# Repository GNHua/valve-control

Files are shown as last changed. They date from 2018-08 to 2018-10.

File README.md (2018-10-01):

# valve-control

Use Arduino Uno to control solenoid valves.  
Follow the steps below to set up your own valve control station.

## Purchase

### Solenoid Valves

* [Clippard, E310C-2C012, 10 mm N-C 3-way Valve, In-line Connector w/LED, 0.030" Orifice, 1.3W, 12 VDC](http://www.clippard.com/part/E310C-2C012)
* [Valve connector cable](http://www.clippard.com/products/electronic-valve-10mm-connector)
* [Manifold](http://www.clippard.com/products/electronic-valve-10mm-manifolds)

Details can be found on page 215-221 in [Clippard Full-line Catalog](http://www.clippard.com/downloads/PDF_Documents/Clippard%20Full%20Line%20Catalog/Clippard%20Full-Line%20Catalog.pdf)

### Send [PCB design](https://github.com/GNHua/valve-control/raw/master/pcb_layout/plots.zip) Out For Manufacturing

* Highly recommend [JLCPCB](https://jlcpcb.com/). Fabrication and shipping took ~1 week for me in the U.S.
* If you choose JLCPCB, go [here](https://jlcpcb.com/quote), upload [plots.zip](pcb_layout/plots.zip), and leave everything else as default.
* If you have access to a PCB baking oven, buying a SMT-Stencil will save you a lot of time for soldering. If not, all the components can still be soldered by hand.

| Top Layer | Bottom Layer |
| --- | --- |
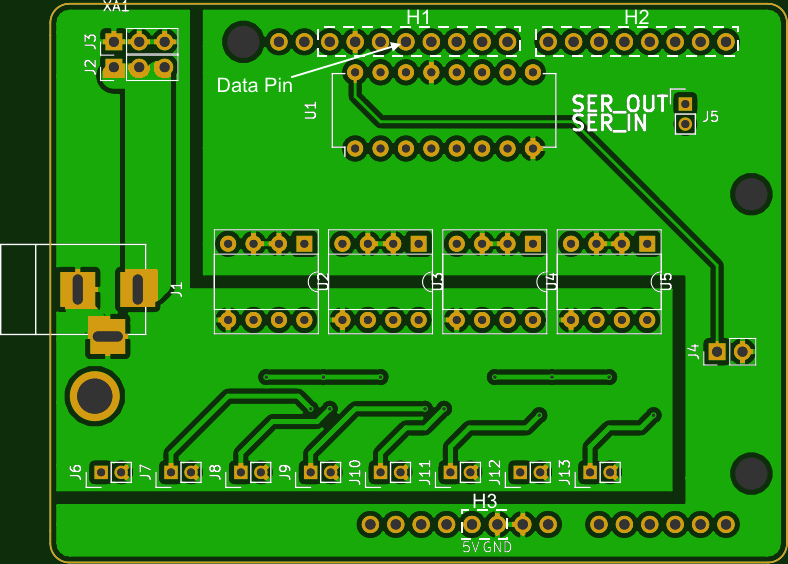
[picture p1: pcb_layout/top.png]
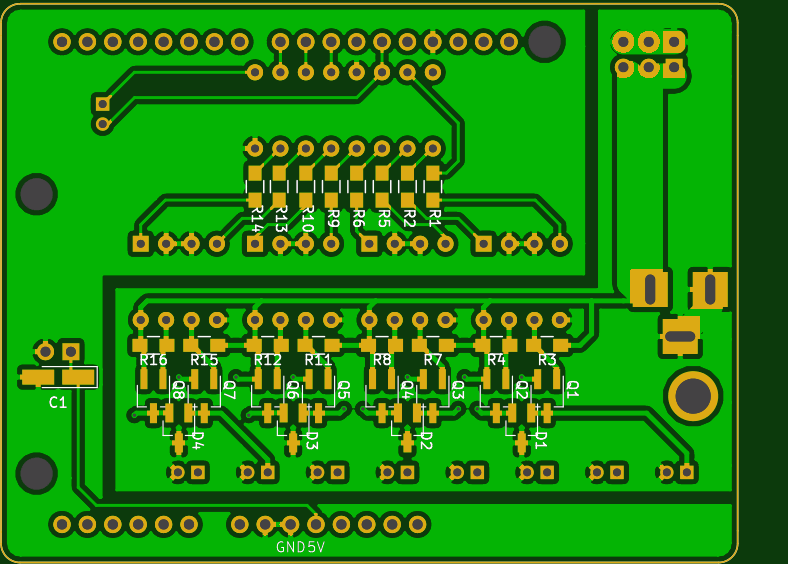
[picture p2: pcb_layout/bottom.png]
|  |  |

### Electrical Components To Buy

| Part | Label on PCB | Qty. (per PCB) | Purchase |
| ---- | :--- | :---: | :---: |
| [Shift register, SN74HC595N](https://www.digikey.com/product-detail/en/texas-instruments/SN74HC595N/296-1600-5-ND/277246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) | plug on the DIP socket (U1) | 1 | [link](https://www.digikey.com/product-detail/en/texas-instruments/SN74HC595N/296-1600-5-ND/277246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)
| [Optoisolator, HCPL 2731](https://www.digikey.com/product-detail/en/on-semiconductor/HCPL2731/HCPL2731QT-ND/31642) | plug on the DIP sockets (U2-U5) | 4 | [link](https://www.digikey.com/product-detail/en/on-semiconductor/HCPL2731/HCPL2731QT-ND/31642) |
| [Resistor, 2.32 k&Omega;, package 0805](https://www.digikey.com/product-detail/en/stackpole-electronics-inc/RMCF0805FT2K32/RMCF0805FT2K32DKR-ND/1943295) | R1-R16 | 16 | [link](https://www.digikey.com/product-detail/en/stackpole-electronics-inc/RMCF0805FT2K32/RMCF0805FT2K32DKR-ND/1943295) |
| [Common anode diode](https://www.digikey.com/product-detail/en/diodes-incorporated/BAT54AT-7-F/BAT54AT-FDICT-ND/821941) | D1-D4 | 4 | [link](https://www.digikey.com/product-detail/en/diodes-incorporated/BAT54AT-7-F/BAT54AT-FDICT-ND/821941) |
| [PMOS](https://www.digikey.com/product-detail/en/toshiba-semiconductor-and-storage/SSM3J338RLF/SSM3J338RLFCT-ND/5810258) | Q1-Q8 | 8 | [link](https://www.digikey.com/product-detail/en/toshiba-semiconductor-and-storage/SSM3J338RLF/SSM3J338RLFCT-ND/5810258) |
| [1 uF capacitor, package 0805, voltage rating 10V](https://www.digikey.com/product-detail/en/yageo/CC0805KKX7R6BB105/311-1458-1-ND/2833764) | C1 | 1 | [link](https://www.digikey.com/product-detail/en/yageo/CC0805KKX7R6BB105/311-1458-1-ND/2833764) |
| [DIP socket, 2x8](https://www.digikey.com/product-detail/en/assmann-wsw-components/A-16-LC-TT/AE9992-ND/821746) | U1 | 1 | [link](https://www.digikey.com/product-detail/en/assmann-wsw-components/A-16-LC-TT/AE9992-ND/821746) |
| [DIP socket, 2x4](https://www.digikey.com/product-detail/en/assmann-wsw-components/A-08-LC-TT/AE9986-ND/821740) | U2-U5 | 4 | [link](https://www.digikey.com/product-detail/en/assmann-wsw-components/A-08-LC-TT/AE9986-ND/821740) |
| [Stacking headers](https://www.digikey.com/products/en?mpart=85&v=1528) | J2-J4, H1, H2 | 1 | [link](https://www.digikey.com/products/en?mpart=85&v=1528) |
| [Connector, Molex 50212-8000](https://www.digikey.com/product-detail/en/molex-llc/50212-8000/WM4561CT-ND/2524899) | N/A | 18 | [link](https://www.digikey.com/product-detail/en/molex-llc/50212-8000/WM4561CT-ND/2524899) |
| [Connector housing, Molex 0873690200](https://www.digikey.com/product-detail/en/molex-llc/0873690200/WM10118-ND/3264531) | N/A | 9 | [link](https://www.digikey.com/product-detail/en/molex-llc/0873690200/WM10118-ND/3264531) |
| [JST header, Molex 0894010210](https://www.digikey.com/products/en?keywords=0894010210) | J5-J13 | 9 | [link](https://www.digikey.com/products/en?keywords=0894010210) |
| [2.5 mm barrel jack, 5A max, CUI PJ-057BH ](https://www.digikey.com/product-detail/en/cui-inc/PJ-057BH/CP-057BH-ND/1644602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) | J1 | 1 for each setup | [link](https://www.digikey.com/product-detail/en/cui-inc/PJ-057BH/CP-057BH-ND/1644602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) |

## Download

Download [zip](https://github.com/GNHua/valve-control/archive/master.zip) and extract all files.

## Prepare Software

### Flash Arduino Uno

* Connect an Arduino Uno to computer via USB
* Download and Install [Arduino IDE](https://www.arduino.cc/en/Main/Software)
* Open `arduino_valve_control.ino` in `arduino_valve_control` folder with Arduino IDE
* Select USB port: `Tools` > `Port`
* Click `Upload` (the right arrow at the top left corner)
* Wait for uploading to complete

### Python

* Download and Install Python 3.6
  * The Python distribution, [Anaconda](https://www.anaconda.com/download) is recommended, because it comes with pre-installed packages. 
  * Note: On Windows, the directory of installed Python must be added to environment variable. 
* Install Python dependencies
  * Windows: double click `platforms/windows/setup.bat`
  * MacOSX: `$ bash <path to>/platforms/macosx/setup.sh`

## Soldering

(ADD photos of top and bottom layer after soldering)

Solder all the components according to the [table above](#Electrical-Components-To-Buy). The surface mount components are soldered to the bottom layer, while the rest are mounted on the top layer.

### Stacking Headers

In the [table above](#Electrical-Components-To-Buy), the [stacking headers](https://www.digikey.com/products/en?mpart=85&v=1528) contains the following headers.

| Stacking Header | Label on PCB | Qty. |
| --- | :--- | :--: |
| 1 x 10 | cut out a 1x2 for J4 | 1 |
| 1 x  8 | H1, H2 | 2 |
| 1 x  6 | | 2 |
| 2 x  3 | J2+J3 | 1 |

### H3 - 5V and GND

Because the JST headers at J11 and J12 block H3 on the top layer, I would do the following:

1. Cut a 1x2 stacking header out of an unused one
2. Solder it on H3 from the bottom layer
3. Cut off the female portion on the top layer
4. Put more solder from the top layer

### Barrel Jack

Each setup only needs one barrel jack to connect to a 12 V power supply. The barrel jack can be soldered on any one of the boards.

## Assembly

### Shift Register and Optoisolators

(The images shown below are all taken for the previous PCB design, which is marginally different from the current design.)

After soldering, plug the shift register and optoisolators into their corresponding DIP sockets. Refer to the following image for their orientation.

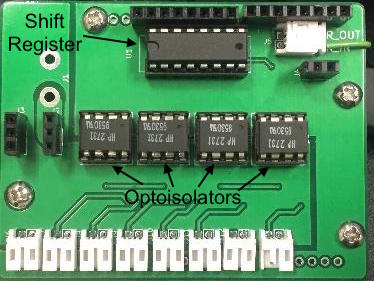
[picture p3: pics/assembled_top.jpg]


### Stacking PCBs

#### For the inpatient

1. Bend or remove the data pins on all boards except Board 1. See the left image below.
2. Make a connector for serial input and serial output. See the right image below.
3. Stack the PCBs and plug in the connector just made.

| Data Pin | Serial Input/Output |
| --- | --- |
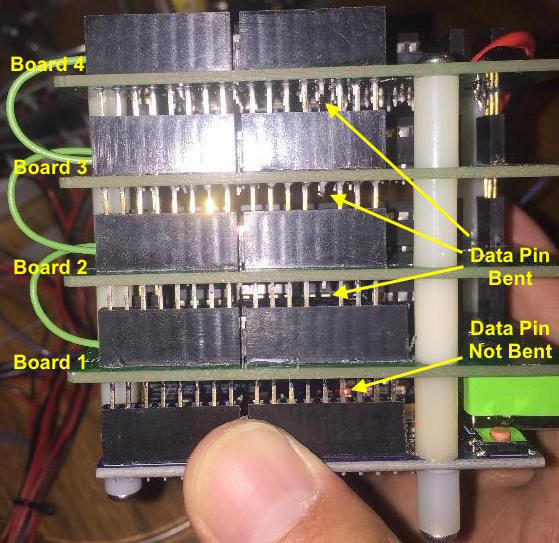
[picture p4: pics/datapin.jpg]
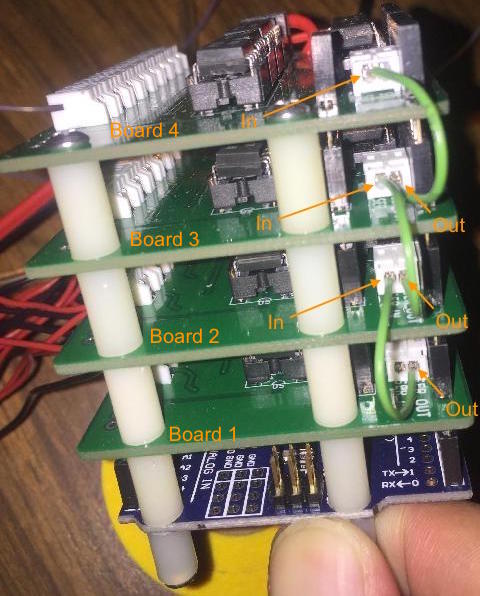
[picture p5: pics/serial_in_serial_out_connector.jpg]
|  |  |

#### Details

In the images above, there are 4 boards stacked on an Arduino Uno.  
Each board provides 8 solenoid valve connectors, and the current design supports up to 6 boards.  
**Before putting the boards together, the data pins on all boards except Board 1 must be bent or removed.**
This is because the data pin connects to the serial input of shift register.
On Board 1, the shift register receives data from the Arduino directly.
For the Board 2-n, their shift registers must have its serial input connected to the serial output of board right beneath it.

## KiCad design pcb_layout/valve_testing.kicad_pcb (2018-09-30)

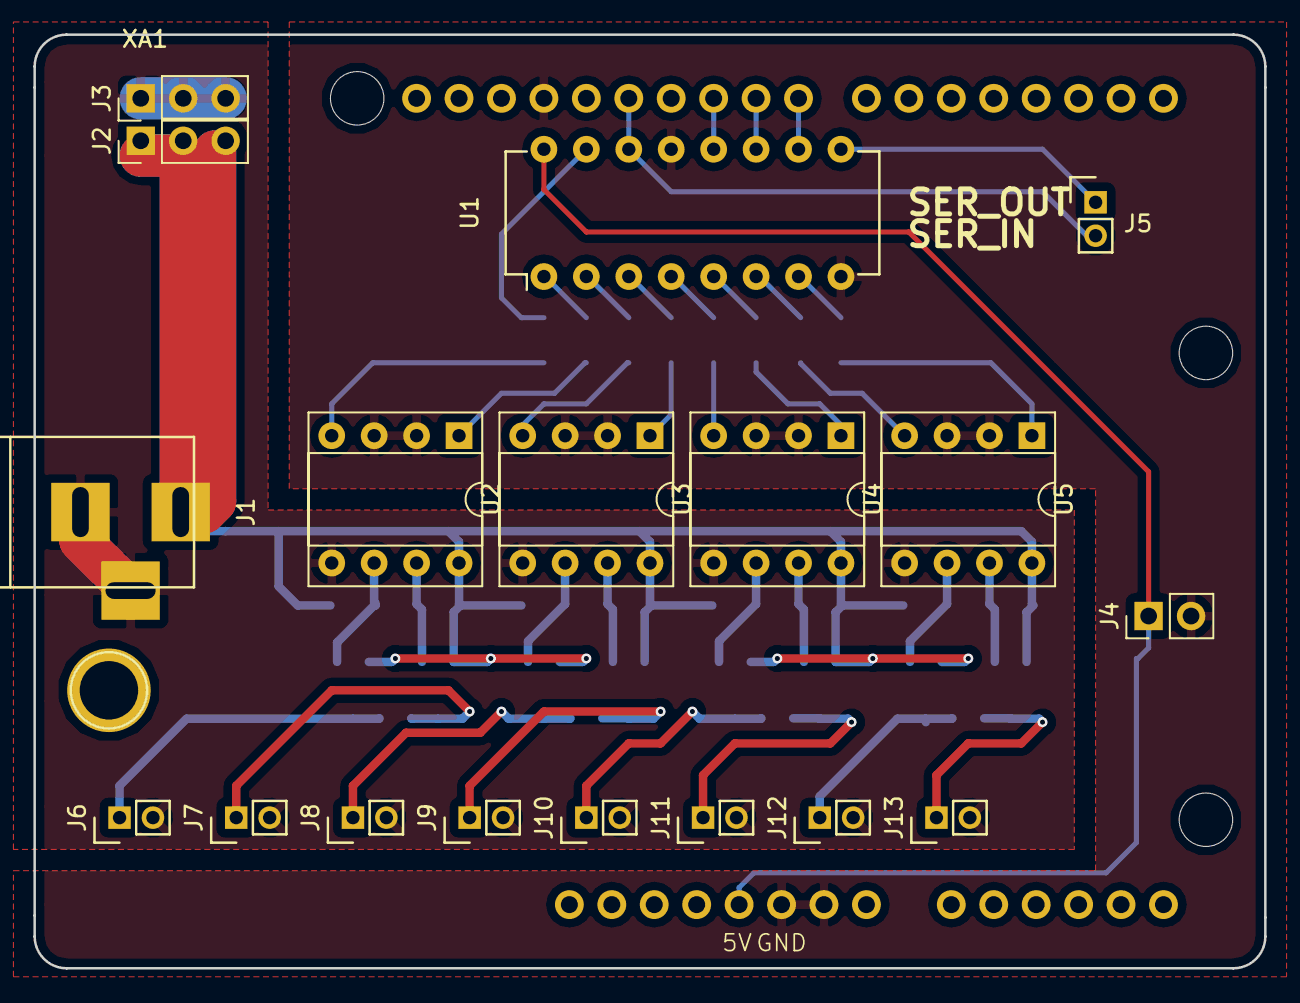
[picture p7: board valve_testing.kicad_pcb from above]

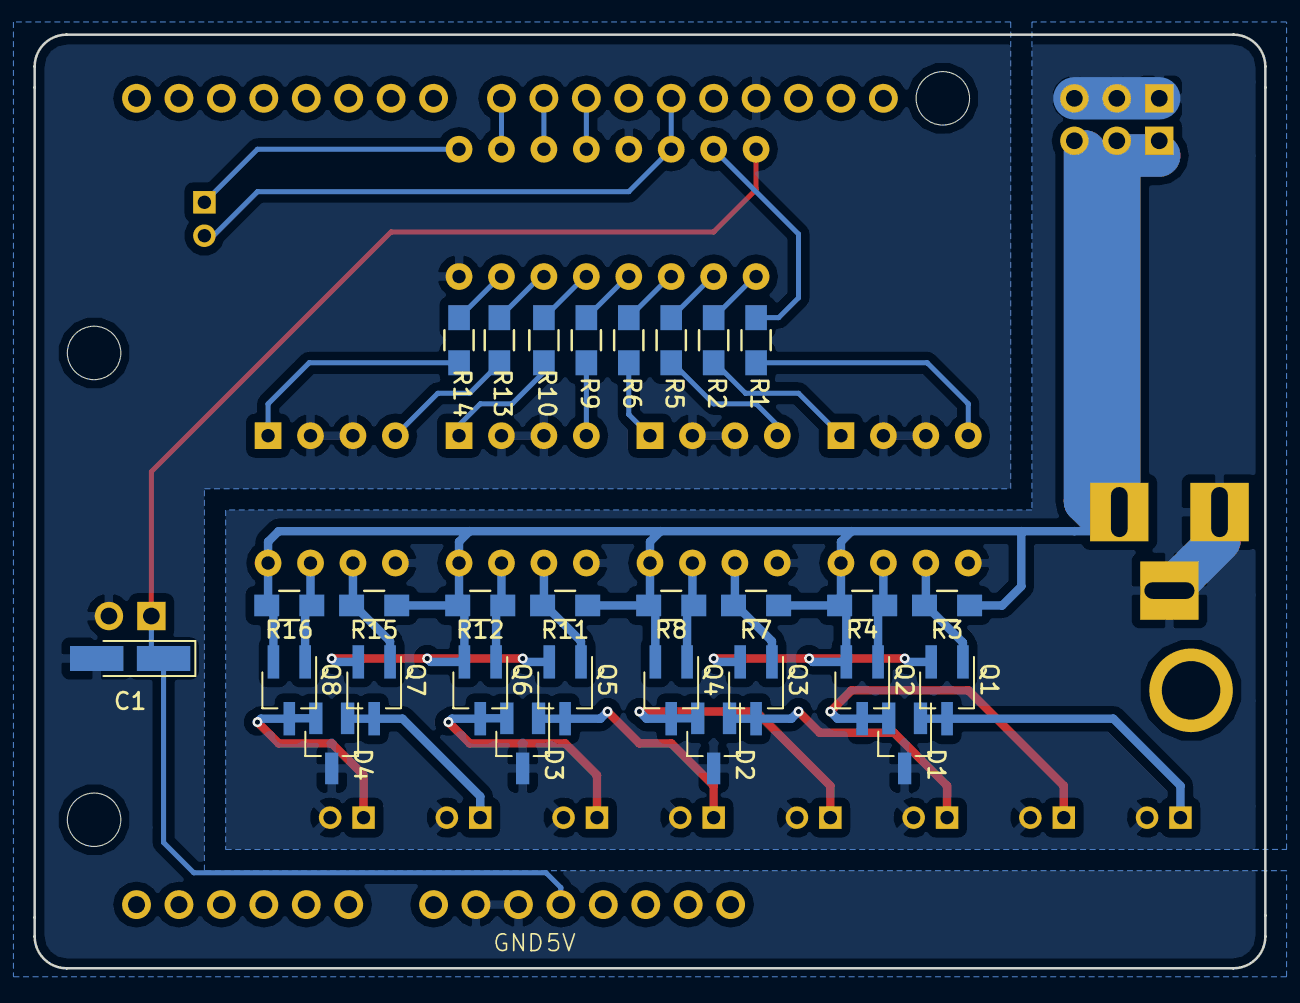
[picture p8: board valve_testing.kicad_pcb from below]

Board: 2 copper layers, 73.7 x 55.9 mm, 48 parts (29 on the bottom side), 40 nets.

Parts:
C1: 1u; CP_Tantalum_Case-A_EIA-3216-18_Hand
D1, D2, D3, D4: D_Schottky_x2_ACom_KKA; SOT-23_Handsoldering
J1: Barrel_Jack; BARREL_JACK
J2, J3: Conn_01x04; Pin_Header_Straight_1x03_Pitch2.54mm
J4: Conn_01x02; Pin_Header_Straight_1x02_Pitch2.54mm
J5, J6, J7, J8, J9, J10, J11, J12, J13: Conn_01x02; Pin_Header_Straight_1x02_Pitch2.00mm
Q1, Q2, Q3, Q4, Q5, Q6, Q7, Q8: Q_PMOS_GSD; SOT-23W_Handsoldering
R1, R2, R3, R4, R5, R6, R7, R8, R9, R10, R11, R12, R13, R14, R15, R16: 2.32k; R_0805_HandSoldering
U1: 74HC595; DIP-16_W7.62mm
U2, U3, U4, U5: HCPL2731; DIP-8_W7.62mm_Socket
XA1: Arduino_Uno_Shield

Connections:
/QA: R1.1, U1.15
/QB: R2.1, U1.1
/QC: R5.1, U1.2
/QD: R6.1, U1.3
/QE: R9.1, U1.4
/QF: R10.1, U1.5
/QG: R13.1, U1.6
/QH: R14.1, U1.7
/SRCLR: U1.10, XA1.D8
/clockPin: U1.11, XA1.D9
/dataPin: J5.2, U1.14, XA1.D12
/latchPin: U1.12, XA1.D10
GND: C1.2, D1.3, D2.3, D3.3, D4.3, J1.2, J1.3, J3.1, J3.2, J3.3, J4.2, J6.2, J7.2, J8.2, J9.2, J10.2, J11.2, J12.2, J13.2, U1.8, U1.13, U2.2, U2.3, U2.5, U3.2, U3.3, U3.5, U4.2, U4.3, U4.5, U5.2, U5.3, U5.5, XA1.GND1, XA1.GND2, XA1.GND3
unnamed: D1.1, J6.1, Q1.3
unnamed: D1.2, J7.1, Q2.3
unnamed: D2.1, J8.1, Q3.3
unnamed: D2.2, J9.1, Q4.3
unnamed: D3.1, J10.1, Q5.3
unnamed: D3.2, J11.1, Q6.3
unnamed: D4.1, J12.1, Q7.3
unnamed: D4.2, J13.1, Q8.3
unnamed: J5.1, U1.9
unnamed: Q1.1, R3.2, U2.6
unnamed: Q2.1, R4.2, U2.7
unnamed: Q3.1, R7.2, U3.6
unnamed: Q4.1, R8.2, U3.7
unnamed: Q5.1, R11.2, U4.6
unnamed: Q6.1, R12.2, U4.7
unnamed: Q7.1, R15.2, U5.6
unnamed: Q8.1, R16.2, U5.7
unnamed: R1.2, U2.4
unnamed: R2.2, U2.1
unnamed: R5.2, U3.4
unnamed: R6.2, U3.1
unnamed: R9.2, U4.4
unnamed: R10.2, U4.1
unnamed: R13.2, U5.4
unnamed: R14.2, U5.1
VCC: C1.1, J4.1, U1.16, XA1.5V1
Vcc_12V: J1.1, J2.1, J2.2, J2.3, Q1.2, Q2.2, Q3.2, Q4.2, Q5.2, Q6.2, Q7.2, Q8.2, R3.1, R4.1, R7.1, R8.1, R11.1, R12.1, R15.1, R16.1, U2.8, U3.8, U4.8, U5.8

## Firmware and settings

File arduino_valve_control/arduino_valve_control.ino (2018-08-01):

#include <EEPROM.h>

#include "SoftReset.h"
#include "defaults.h"

#define MYPORT PORTB
#define SRCLR 8
#define dataPin 12
#define clockPin 9
#define latchPin 10
#define SRCLRBitLoc (SRCLR-8)
#define dataPinBitLoc (dataPin-8)
#define clockPinBitLoc (clockPin-8)
#define latchPinBitLoc (latchPin-8)

uint8_t regNum;    // number of registers used
char* currentState;        // keep track of shift register outputs
char* masks;
char* operations;         // 100 different operations max
uint8_t* phase;      // a list of phase describes the valve actuating sequence
uint8_t* beforePhase;
uint8_t* afterPhase;
volatile uint16_t currentPhaseIndex;        // current phase
uint8_t totalPhases;     // total number of phases
uint8_t totalBeforePhases;
uint8_t totalAfterPhases;
volatile uint32_t currentCycle = 0;
uint32_t totalCycles = 0;
bool longTimerEnabled;
uint32_t intervalMillis;
uint32_t previousMillis;

const uint8_t serStrLen = 28;   // max length of serial input string, baudrate 115200 for 2 ms
char serInStr[ serStrLen ];     // array that will hold the serial input string

void fastShiftOut(char* data, uint8_t length)
{
  // reset clock pin and latch pin
  MYPORT &= ~(1 << latchPinBitLoc);
  
  for(uint8_t i=0; i<length; i++) {
    for(int8_t j=7; j>=0; j--) {
      MYPORT &= ~(1 << clockPinBitLoc);
      
      // set data pin
      char dataBit = (data[i] >> j) & B00000001;
      // change the data pin
      MYPORT ^= (MYPORT ^ -(uint8_t)dataBit) & (1 << dataPinBitLoc);
      
      MYPORT |= (1 << clockPinBitLoc);
    }
  }
  
  // create a rising edge at latch pin
  MYPORT |= (1 << latchPinBitLoc);
}

void controlValves(char* data, char* mask, uint8_t length)
{
  for(uint8_t i=0; i<length; i++) {
    data[i] &= mask[i];
    currentState[i] &= ~mask[i];
    currentState[i] |= data[i];
  }
  
  fastShiftOut(currentState, length);
}

void start()
{
  // do nothing if it is already running
  if (((TIMSK1 >> OCIE1A) & B00000001) || longTimerEnabled) {
    return ;
  }

  runBeforeAfterPhase(beforePhase, totalBeforePhases);

  if (totalPhases) {
    currentPhaseIndex = 0;
    currentCycle = 0;
    if (intervalMillis <= 200) {
      float freq = 1000 / intervalMillis;
      noInterrupts();
      OCR1A = (uint16_t)(1.6e7 / 64 / freq);
      TCNT1 = 0;
      TIMSK1 |= (1 << OCIE1A);
      interrupts();
    } else {
      longTimerEnabled = true;
      previousMillis = millis();
    }
  }
}

/////////////////////////////////////////////////

// use hardware timer for interval equal to or below 200 ms
ISR(TIMER1_COMPA_vect)  // timer compare interrupt service routine
{
  controlValves(operations+phase[currentPhaseIndex]*regNum, masks+phase[currentPhaseIndex]*regNum, regNum);
  currentPhaseIndex++;

  if (currentPhaseIndex >= totalPhases) {
    currentPhaseIndex = 0;
    currentCycle++;
  }

  // disable timer compare interrupt if all cycles are done
  if (totalCycles != 0 && currentCycle >= totalCycles) {
    TIMSK1 &= ~(1 << OCIE1A);
    currentCycle = 0;
    runBeforeAfterPhase(afterPhase, totalAfterPhases);
  }
}

// use long timer for interval above 200 ms
void runLongTimer()
{
  uint32_t currentMillis = millis(); // grab current time
  if (longTimerEnabled && (uint32_t)(currentMillis - previousMillis) >= intervalMillis) {
    controlValves(operations+phase[currentPhaseIndex]*regNum, masks+phase[currentPhaseIndex]*regNum, regNum);
    currentPhaseIndex++;
    
    // save the "current" time
    previousMillis = currentMillis;
    
    if (currentPhaseIndex >= totalPhases) {
      currentPhaseIndex = 0;
      currentCycle++;
    }
    
    // disable long timer if all cycles are run
    if (totalCycles != 0 && currentCycle >= totalCycles) {
      longTimerEnabled = false;
      currentCycle = 0;
      runBeforeAfterPhase(afterPhase, totalAfterPhases);
    }
  }
}
/////////////////////////////////////////////////

void runBeforeAfterPhase(uint8_t* phase, uint8_t length)
{
  for(uint8_t i=0; i<length; i++) {
    controlValves(operations+phase[i]*regNum, masks+phase[i]*regNum, regNum);
    delay(intervalMillis);
  }
}

void stop()
{
  TIMSK1 &= ~(1 << OCIE1A);
  longTimerEnabled = false;
  runBeforeAfterPhase(afterPhase, totalAfterPhases);

  Serial.write((char*)(&currentCycle), sizeof(currentCycle));
  Serial.write(currentState, regNum);
  Serial.println();
  currentCycle = 0;
}

void clearShiftRegister()
{
  // do nothing if it is already running
  if (((TIMSK1 >> OCIE1A) & B00000001) || longTimerEnabled) {
    return ;
  }
  
  MYPORT &= ~(1 << latchPinBitLoc);
  MYPORT &= ~(1 << clockPinBitLoc);
  MYPORT &= ~(1 << SRCLRBitLoc);
  MYPORT |= (1 << clockPinBitLoc);
  MYPORT |= (1 << SRCLRBitLoc);
  MYPORT |= (1 << latchPinBitLoc);
  
  // reset currentState
  memset(currentState, 0, regNum);
}

void clear()
{
  // do nothing if it is already running
  if (((TIMSK1 >> OCIE1A) & B00000001) || longTimerEnabled) {
    return ;
  }
  
  clearShiftRegister();
  uint8_t operationNum = EEPROM.read(OPERATION_NUM_ADDR);
  uint8_t phaseNum = EEPROM.read(PHASE_NUM_ADDR);
  uint8_t beforePhaseNum = EEPROM.read(BEFORE_PHASE_NUM_ADDR);
  uint8_t afterPhaseNum = EEPROM.read(AFTER_PHASE_NUM_ADDR);
  memset(operations, 0, operationNum*regNum);
  memset(masks, 0, operationNum*regNum);
  memset(phase, 0, phaseNum);
  memset(beforePhase, 0, beforePhaseNum);
  memset(afterPhase, 0, afterPhaseNum);
  
  currentPhaseIndex = 0;        // current phase
  totalPhases = 0;              // total number of phases
  totalBeforePhases = 0;
  totalAfterPhases = 0;
  currentCycle = 0;
  totalCycles = 0;
}

void setup()
{
  uint8_t flag = EEPROM.read(VERSION_ADDR);
  if (flag != VERSION) {
    EEPROM.update(VERSION_ADDR, (byte)VERSION);
    EEPROM.update(REG_NUM_ADDR, (byte)REG_NUM);
    EEPROM.update(OPERATION_NUM_ADDR, (byte)OPERATION_NUM);
    EEPROM.update(PHASE_NUM_ADDR, (byte)(PHASE_NUM));
    EEPROM.update(BEFORE_PHASE_NUM_ADDR, (byte)(BEFORE_PHASE_NUM));
    EEPROM.update(AFTER_PHASE_NUM_ADDR, (byte)(AFTER_PHASE_NUM));
  }
  
  pinMode(SRCLR, OUTPUT);
  MYPORT |= (1 << SRCLRBitLoc);
  
  pinMode(dataPin,  OUTPUT);
  pinMode(clockPin, OUTPUT);
  pinMode(latchPin, OUTPUT);
  
  // initialize timer1 
  noInterrupts();     // disable all interrupts
  TCCR1A = 0;
  TCCR1B = 0;
  TCCR1B |= (1 << WGM12);                 // CTC mode
  TCCR1B |= (1 << CS11) | (1 << CS10);    // 64 prescaler 
  TIMSK1 &= ~(1 << OCIE1A);               // disable timer compare interrupt
  interrupts();                           // enable all interrupts
  
  longTimerEnabled = false;

  regNum = EEPROM.read(REG_NUM_ADDR);
  uint8_t operationNum = EEPROM.read(OPERATION_NUM_ADDR);
  uint8_t phaseNum = EEPROM.read(PHASE_NUM_ADDR);
  uint8_t beforePhaseNum = EEPROM.read(BEFORE_PHASE_NUM_ADDR);
  uint8_t afterPhaseNum = EEPROM.read(AFTER_PHASE_NUM_ADDR);
  currentState = (char*)malloc(regNum);
  masks = (char*)malloc(operationNum*regNum);
  operations = (char*)malloc(operationNum*regNum);
  phase = (uint8_t*)malloc(phaseNum); 
  beforePhase = (uint8_t*)malloc(beforePhaseNum);
  afterPhase = (uint8_t*)malloc(afterPhaseNum);
  clear();
  
  Serial.begin(115200);
  delay(2000); //To allow time for serial port to begin
}

void loop()
{
  GetSerialInput();
  runLongTimer();
}

void GetSerialInput() {
  uint8_t strSize = readSerialString();
  if (strSize) {
    switch (serInStr[0]) {
      case 0x00: // send the number of shift registers
      {
        // byte 1: regNum
        if (regNum != EEPROM.read(REG_NUM_ADDR)) {
          EEPROM.update(REG_NUM_ADDR, serInStr[1]);
          regNum = EEPROM.read(REG_NUM_ADDR);
          soft_restart();
        }
        break;
      }
      case 0x01: // send the total phase number in one cycle
        // byte 1: totalPhases
        // byte 2: totalBeforePhases
        // byte 3: totalAfterPhases
        memcpy(&totalPhases, serInStr+1, sizeof(totalPhases));
        memcpy(&totalBeforePhases, serInStr+2, sizeof(totalBeforePhases));
        memcpy(&totalAfterPhases, serInStr+3, sizeof(totalAfterPhases));
        break;
      case 0x02: // send data in `operations`
      {
        // byte 1: offset in `operations`
        // byte 2-(2+regNum): data
        // byte (2+regNum)-(2+regNum*2): mask
        uint8_t i = serInStr[1];
        memcpy(operations+i*regNum, serInStr+2, regNum);
        memcpy(masks+i*regNum, serInStr+2+regNum, regNum);
        break;
      }
      case 0x03: // send data in `phase`
      {
        // byte 1: offset in `phase`; byte 2-?: data
        uint8_t i = serInStr[1];
        memcpy(phase+i, serInStr+2, strSize-2);
        break;
      }
      case 0x04: // send data in `beforePhase`
      {
        // byte 1: offset in `beforePhase`; byte 2-?: data
        uint8_t i = serInStr[1];
        memcpy(beforePhase+i, serInStr+2, strSize-2);
        break;
      }
      case 0x05: // send data in `afterPhase`
      {
        // byte 1: offset in `afterPhase`; byte 2-?: data
        uint8_t i = serInStr[1];
        memcpy(afterPhase+i, serInStr+2, strSize-2);
        break;
      }
      case 0x06: // start
      {
        // byte 1-4: totalCycles; byte 5-8: intervalMillis
        memcpy(&totalCycles, serInStr+1, sizeof(totalCycles));
        memcpy(&intervalMillis, serInStr+1+sizeof(totalCycles), sizeof(intervalMillis));
        start();
        break;
      }
      case 0x07: // stop
        stop();
        break;
      case 0x08: // control valves
      {
        // byte 1-(1+regNum): valve controls 
        // byte (1+regNum)-(1+regNum*2): mask
        controlValves(serInStr+1, serInStr+1+regNum, regNum);
        break;
      }
      case 0x09: // clear shift register outputs
      {
        clearShiftRegister();
        break;
      }
      case 0x0A:
      {
        clear();
        break;
      }
      case 0x0B:
      {
        uint8_t addr = serInStr[1];
        for(uint8_t i=2; i<strSize; i++) {
          EEPROM.update(addr, serInStr[i]);
          addr++;
        }
        soft_restart();
        break;
      }
      case 0x0C:
      {
        soft_restart();
        break;
      }
      case 0x0D:
      {
        Serial.write(currentState, regNum);
        Serial.write((char*)(&totalCycles), sizeof(totalCycles));
        Serial.write((char*)(&currentCycle), sizeof(currentCycle));
        Serial.println();
        break;
      }
      case 0x0E:
      {
        for(uint8_t i=0; i<256; i++) {
          byte res = EEPROM.read(i);
          if (res == 0xFF) {
            break;
          } else {
            Serial.write(res);
          }
        }
        Serial.println();
        break;
      }
      default:
        break;
    }
  }
}

uint8_t readSerialString() {
  if(!Serial.available()) {
    return 0;
  }
  delay(2);  // wait a little for serial data
  memset( serInStr, 0, sizeof(serInStr) ); // set it all to zero (look up Arduino memset function)
  uint8_t i = 0;
  while(Serial.available() && i<serStrLen ) {
    serInStr[i] = Serial.read();   // FIXME: doesn't check buffer overrun
    i++;
  }

  return i;  // return number of chars read
} //readSerialString

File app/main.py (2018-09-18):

import os
import sys
from PyQt5 import QtWidgets, uic
import serial.tools.list_ports
import urllib.request
import glob
import shutil
import zipfile
import webbrowser

from app import __version__
from app.ui.connect import UsbPortsTableDialog
from app.ui.flow_layout import FlowLayout
from app.ui.built_in_program_dialog import ToggleValveDialog, FivePhasePumpDialog
from app.valve_control import ValveControlDevice, ToggleValveCycle, FivePhasePumpCycle

APP_DIR = os.path.dirname(os.path.abspath(__file__))
ROOT_DIR = os.path.abspath(os.path.join(APP_DIR, '..'))
Ui_MainWindow, QMainWindow = uic.loadUiType(os.path.join(APP_DIR, 'ui', 'main.ui'))


class MainWindow(QMainWindow, Ui_MainWindow):

    def __init__(self):
        super().__init__()
        self.setupUi(self)
        self.flowLayoutValveControl = FlowLayout(parent=self.frameValveControl)
        with open(os.path.join(APP_DIR, 'ui', 'style_sheet.txt'), 'r') as f:
            styleSheet = f.read()
        self.setStyleSheet(styleSheet)

        self.dir = APP_DIR

    def getUsbPort(self):
        ports = serial.tools.list_ports.comports()
        dialog = UsbPortsTableDialog(ports=ports)
        if dialog.exec_() == QtWidgets.QDialog.Accepted:
            index = dialog.tableViewUsbPorts.selectedIndexes()[0]
            if index:
                port = ports[index.row()].device
                self.setDevice(port=port)
            else:
                QtWidgets.QMessageBox.critical(
                    self,
                    'Warning!',
                    'Please select a USB port\n',
                    QtWidgets.QMessageBox.Ok)
                self.getUsbPort()
        else:
            sys.exit()

    def setDevice(self, port):
        self.device = ValveControlDevice(port=port)
        regNum = self.device.settings['REG_NUM']
        for i in range(1, 8*regNum+1):
            checkBox = QtWidgets.QCheckBox(str(i))
            self.flowLayoutValveControl.addWidget(checkBox)
            checkBox.toggled[bool].connect(self.addValveControl(i))
            self.__dict__[f'checkBoxValve{i}'] = checkBox
        self.__dict__[f'actionSR{regNum}'].setChecked(True)
        self.menuSerial.setTitle(f'Port: "{port}"')
        self.connectUi()

    def addValveControl(self, i):
        def func(valveOn):
            self.device.controlSingleValve(i, valveOn)
        return func

    def connectUi(self):
        self.actionGroupSR = QtWidgets.QActionGroup(self.menuShift_Register)
        for i in range(1, 7):
            self.actionGroupSR.addAction(self.__dict__[f'actionSR{i}'])

        self.toolButtonProgram.clicked.connect(self.uploadProgram)
        self.pushButtonStart.clicked.connect(self.start)
        self.pushButtonStop.clicked.connect(self.stop)
        self.pushButtonLoadBuiltIn.clicked.connect(self.loadBuiltInProgram)
        self.actionOpen.triggered.connect(self.uploadProgram)
        self.actionClose.triggered.connect(self.close)
        self.actionRestart_Device.triggered.connect(self.restartDevice)
        self.actionTurn_Off_All.triggered.connect(self.clear)
        self.actionStart.triggered.connect(self.start)
        self.actionStop.triggered.connect(self.stop)
        self.actionGroupSR.triggered.connect(self.changeSR)
        self.actionReset_Input.triggered.connect(self.serialResetInput)
        self.actionReset_Output.triggered.connect(self.serialResetOutput)
        self.actionDocumentation.triggered.connect(self.openGithubRepo)
        self.actionUpdate.triggered.connect(self.update)

    def uploadProgram(self):
        fn, _ = QtWidgets.QFileDialog.getOpenFileName(self, 'Open File', self.dir, 'text (*.txt)')
        self.dir = os.path.dirname(fn)
        if fn:
            wrongLines = self.device.makeProgrammableCycle(fn)
            if wrongLines:
                wrongLines = ', '.join(list(map(str, self.device.programmableCycle.wrongLines)))
                QtWidgets.QMessageBox.critical(
                    self, 'Error!',
                    'Error at line ' + wrongLines,
                    QtWidgets.QMessageBox.Ok)
            else:
                self.lineEditProgram.setText(fn)
                self.device.uploadProgram()

    def start(self):
        if self.lineEditProgram.text():
            cycles = self.spinBoxCycles.value()
            phaseIntervalMillis = self.spinBoxIntervalMillis.value()
            self.device.start(cycles, phaseIntervalMillis)

    def stop(self):
        cycleCompleted, valveStates = self.device.stop()
        regNum = self.device.settings['REG_NUM']
        for i in range(1, 8*regNum+1):
            self.__dict__[f'checkBoxValve{i}'].blockSignals(True)
            self.__dict__[f'checkBoxValve{i}'].setChecked(valveStates[i-1])
            self.__dict__[f'checkBoxValve{i}'].blockSignals(False)

    def loadBuiltInProgram(self):
        valveNum = 8 * self.device.settings['REG_NUM']
        index = self.comboBoxBuiltIn.currentIndex()
        if index == 0:
            dialog = ToggleValveDialog(valveNum=valveNum)
            if dialog.exec_() == QtWidgets.QDialog.Accepted:
                valve = dialog.spinBoxValve.value()
                self.device.loadToggleValveProgram(valve)
                self.lineEditProgram.setText(f'Built-in Prgram: Toggle Valve {valve}')

        elif index == 1:
            dialog = FivePhasePumpDialog(valveNum=valveNum)
            while True:
                if dialog.exec_() == QtWidgets.QDialog.Accepted:
                    inputValve = dialog.spinBoxInputValve.value()
                    DC = dialog.spinBoxDC.value()
                    outputValve = dialog.spinBoxOutputValve.value()

                    # Check if all 3 valves are different.
                    if len(set([inputValve, DC, outputValve])) != 3:
                        QtWidgets.QMessageBox.critical(
                            self, 'Error!',
                            'You must choose 3 different valves!',
                            QtWidgets.QMessageBox.Ok)
                    else:
                        self.device.load5PhasePumpProgram(inputValve, DC, outputValve)
                        self.lineEditProgram.setText(f'Built-in Prgram: 5 Phase Pump ({inputValve}, {DC}, {outputValve})')
                        break
                else:
                    break

    def restartDevice(self):
        self.device.restart()

    def clear(self):
        self.device.clearShiftRegister()
        regNum = self.device.settings['REG_NUM']
        for i in range(1, 8*regNum+1):
            self.__dict__[f'checkBoxValve{i}'].blockSignals(True)
            self.__dict__[f'checkBoxValve{i}'].setChecked(False)
            self.__dict__[f'checkBoxValve{i}'].blockSignals(False)

    def changeSR(self):
        regNum = int(self.menuShift_Register.checkedAction.text())
        if regNum == self.device.settings['REG_NUM']:
            return
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

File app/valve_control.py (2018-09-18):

import serial
import time


class ValveControlBase(serial.Serial):

    def __init__(self, port):
        super().__init__(port=port, baudrate=115200, timeout=1)

        while True:
            try:
                self.reset_input_buffer()
                self.reset_output_buffer()
                self.settings = self.getEEPROMSettings()
                break
            except IndexError:
                time.sleep(1)

    def send(self, command, wait=0):
        if not isinstance(command, bytes):
            command = bytes(command, encoding='ascii')
        self.write(command)
        
        # must wait for at least 50 ms to get response from arduino
        time.sleep(0.01)
        
        if wait:
            time.sleep(wait)
            response = b''
            while self.in_waiting:
                response += self.readline()
            return response

    def setRegNum(self, n):
        """Set number of 8-bit registers. 
        This will restart arduino.
        
        :param int n: number of registers
        """
        self.send(b'\x00' + int(n).to_bytes(1, 'little'))
        time.sleep(1)
        self.settings = self.getEEPROMSettings()

    def setTotalPhases(self, totalPhases, totalBeforePhases, totalAfterPhases):
        """Set total phases. 

        :param int totalPhases: total number of phases
        :param int totalBeforePhases: total number of phases before cycles
        :param int totalAfterPhases: total number of phases after cycles
        """
        byte1 = int(totalPhases).to_bytes(1, 'little')
        byte2 = int(totalBeforePhases).to_bytes(1, 'little')
        byte3 = int(totalAfterPhases).to_bytes(1, 'little')
        self.send(b'\x01' + byte1 + byte2 + byte3)

    def setOperation(self, index, on=(), off=()):
        """Set operation data.
        
        :param int index: phase index in the `state` array in Arduino code
        :param list on: a list of valve numbers (int) to turn on
        :param list off: a list of valve number (int) to turn off
        """
        onBytes = 0
        for i in on:
            onBytes |= (1 << (i-1))
        offBytes = 0
        for i in off:
            offBytes |= (1 << (i-1))
        maskBytes = onBytes | offBytes
        
        data = onBytes.to_bytes(self.settings['REG_NUM'], 'big')
        mask = maskBytes.to_bytes(self.settings['REG_NUM'], 'big')
        self.send(b'\x02' + index.to_bytes(1, 'little') + data + mask)

    def setPhase(self, offset, operationIndex):
        """Copy data to ``phase` array, starting from ``offset``.
        
        :param int offset: offset in the ``phase`` array
        :param list operationIndex: a list of operation index (int)
        """
        data = b''
        for i in operationIndex:
            data += i.to_bytes(1, 'little')
        self.send(b'\x03' + offset.to_bytes(1, 'little') + data)

    def setBeforePhase(self, offset, operationIndex):
        """Copy data to ``phase` array, starting from ``offset``.
        
        :param int offset: offset in the ``beforePhase`` array
        :param list operationIndex: a list of operation index (int)
        """
        data = b''
        for i in operationIndex:
            data += i.to_bytes(1, 'little')
        self.send(b'\x04' + offset.to_bytes(1, 'little') + data)

    def setAfterPhase(self, offset, operationIndex):
        """Copy data to ``phase` array, starting from ``offset``.
        
        :param int offset: offset in the ``afterPhase`` array
        :param list operationIndex: a list of operation index (int)
        """
        data = b''
        for i in operationIndex:
            data += i.to_bytes(1, 'little')
        self.send(b'\x05' + offset.to_bytes(1, 'little') + data)

    def start(self, cycles, phaseIntervalMillis):
        """Start cycles.
        
        :param int cycles: number of cycles to run
        :param int phaseIntervalMillis: the interval in milliseconds between 
                                        different phases in a cycle. NOTE: This 
                                        is the cycle period. 
        """
        cycles = cycles.to_bytes(4, 'little')
        phaseIntervalMillis = phaseIntervalMillis.to_bytes(4, 'little')
        self.send(b'\x06' + cycles + phaseIntervalMillis)

    def stop(self):
        """Stop running cycles"""
        res = self.send(b'\x07', wait=0.2)
        cycleCompleted = int.from_bytes(res[:4], 'little')
        temp = int.from_bytes(res[4:4+self.settings['REG_NUM']], 'big')
        valveStates = []
        for i in range(8*self.settings['REG_NUM']):
            valveStates.append((temp >> i) & 1)
        return cycleCompleted, valveStates

    def controlValves(self, on=(), off=()):
        """Control vlaves manually.
        
        :param list on: a list of valve numbers (int) to turn on
        :param list off: a list of valve numbers (int) to turn off
        """
        onBytes = 0
        for i in on:
            onBytes |= (1 << (i-1))
        offBytes = 0
        for i in off:
            offBytes |= (1 << (i-1))
        maskBytes = onBytes | offBytes
        
        data = onBytes.to_bytes(self.settings['REG_NUM'], 'big')
        mask = maskBytes.to_bytes(self.settings['REG_NUM'], 'big')
        self.send(b'\x08' + data + mask)

    def clearShiftRegister(self):
        """Reset shift register outputs"""
        self.send(b'\x09')

    def clear(self):
        """Reset shift register outputs and all parameters"""
        self.send(b'\x0A')

    def updateEEPROM(self, addr, data):
        """Set the parameters in EEPROM. 
        
        :param int addr: address in EEPROM, range 0-255
        :param data bytes: the data to write onto EEPROM
        """
        self.send(b'\x0B' + int(addr).to_bytes(1, 'little') + data)

    def restart(self):
        """Restart Arduino. 
        It does not do anything to the peripheral circuits. 
        """
        self.send(b'\x0C')

    def getEEPROMSettings(self):
        """Get the settings in EEPROM.
        
        There are 6 bytes in total. 
        Byte 0: EEPROM_RESET_FLAG
        Byte 1: REG_NUM
        Byte 2: STATE_NUM
        Byte 3: PHASE_NUM
        Byte 4: BEFORE_PHASE_NUM
        Byte 5: AFTER_PHASE_NUM
        """
        res = self.send(b'\x0E', wait=0.1)[:-2]
        return {
            'EEPROM_RESET_FLAG': res[0], 
            'REG_NUM': res[1], 
            'STATE_NUM': res[2], 
            'PHASE_NUM': res[3],
            'BEFORE_PHASE_NUM': res[4],
            'AFTER_PHASE_NUM': res[5]
        }
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

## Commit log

2018-08-01 init commit
    [valve_driver.sch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]
2018-08-01 sync valve state when stopped actuating
2018-08-01 fix a small bug
    [arduino_valve_control.ino]
2018-08-10 new pcb
    [valve_driver.sch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]
2018-08-10 resize pcb image
2018-09-30 Add more details on how to solder and assemble
    [valve_testing-B.Cu.gbr, valve_testing-B.Mask.gbr, valve_testing-B.Paste.gbr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]
